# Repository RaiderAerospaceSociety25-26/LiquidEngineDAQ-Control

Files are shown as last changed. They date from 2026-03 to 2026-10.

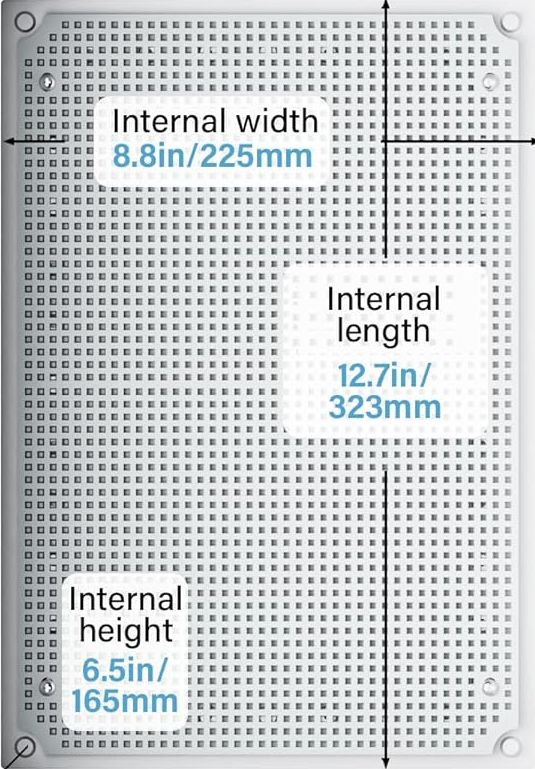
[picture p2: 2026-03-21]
hardware/layout/controlsbox_GEVEELIFE_crop.jpg

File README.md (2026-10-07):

# LiquidEngineDAQ-Control
Repository for DAQ and control system for the liquid engine and test stand being developed by Kyle Markel for the Raider Aerospace Society (RAS) PigeonWorks Liquid Engine Team during the 2025-2026 and 2026-2027 academic years.

For master to-do list, see Kanban board in Teams for the most up-to-date information.

# Firmware
## Firmware Architecture
Plan is to just use Arduino and the common setup and loop structure for the Teensys. The Nucleo will need STM32Cube IDE to be able to flash to both the M7 and M4 chip (there are other ways, but this is the easiest I think). Ideally move to something like FreeRTOS (i.e. X-CUBE-FREERTOS) for the Nucleo board eventually to potentially speed things up.

SPI communication code examples [link](https://www.makerguides.com/master-slave-spi-communication-arduino/#SPI_Master-Slave_Interfacing)

### MCU Function Divisions and Required Libraries
#### Teensy LC/TM
* Functions:
  * Obtain thrust (i.e. load cell) and thermistor data and send it to Nucleo via SPI.
#### Teensy PT
* Functions:
  * Obtain PT data and send it to Nucleo via SPI.
#### Nucleo
* Functions:
  * Receive LC/TM/PT data via two SPI connections
  * Write data to SD card
  * Actuate valves (servo-actuated ball valves) and send ignition signal based on predetermined sequences triggered by T-Beam radio over TX/RX pins
  * Sense overpressures or other issues and send alarms and/or autonomously actuate valves
  * (Maybe: execute automatic safing/depressurization procedures)

# Hardware and Firmware

### MCUs

#### Nucleo-H755ZI-Q
[STMicroelectronics Nucleo-144 H755ZI-Q](https://www.st.com/en/evaluation-tools/nucleo-h755zi-q.html)

Main MCU: STM32H755ZIT6

Secondary MCU: STM32F723IEK6 (I think)

Software required for programming: STM32MX, STM32CubeIDE, STM32CubeProg (STM32CubeProgrammer)

Flashing code to Nucleo board:
* Plug in USB cable to CN1 (the ST-LINK port).
* Have the debug configuration set in STM32CubeIDE.
* Build both M4 and M7 projects.
* Run M4 project -> this will upload the new M4 code to the M4 chip, but will also stop all operations because of the timing/sync relationship between M7 and M4.
* Run M7 project -> this will upload the new M7 code to the M7 chip and will sync and restart the M4 chip. Now all code is running correctly.
* There is probably a more streamlined way to do this so you only have to upload code once; I have not yet found it though. 

Roughly following this tutorial for coding the STM32: STM32Cube IDE tutorial for multiple cores [link](https://blog.embeddedexpert.io/?p=4075) 

Some info about setting up FreeRTOS on the Nucleo [link](https://dds-demonstrators.readthedocs.io/en/latest/Teams/2.Demonstra-Tors/7.NucleoDDS/DDSFreeRTOS.html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)

Relevant timer info [link](https://community.st.com/stm32cubemx-mcus-29/trouble-changing-timebase-to-something-other-than-systick-24703)

Info on requiring a different timebase when running with RTOS [link](https://community.st.com/stm32cubemx-mcus-29/code-generated-by-stm32cubemx-sets-the-hal-timebase-isr-priority-incorrectly-when-using-freertos-is-it-really-necessary-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)

SPI1: PT Teensy

SPI3: LC/TM Teensy

I2C1: Servo shield

PE14: Ignition relay GPIO pin

LPUART1: Radio I/O (UART tutorial with STM32: https://controllerstech.com/stm32-uart-1-configure-uart-transmit-data/)

QSPI: SD card board (CN10: 13, 15, 21, 23 | PG6, PB2, PD12, PD11)

LEDs: green (1 - PB0), red (3 - PB14), yellow (2 - PE1) [info from schematic: https://www.st.com/resource/en/schematic_pack/mb1363-h755ziq-d01_schematic.pdf]

### ADS1256 Notes
ADS1256 analog signal input maxes out at AVDD minus 2V (so 3V maximum analog signal) if using self-calibration routines with the buffer. If we have the capability to perform calibration and write calibration values directly to the register, we could bypass this and use the full range (analog signals accepted up to AVDD), but this would likely be fairly difficult. HOWEVER, it looks like the buffer is the issue. The buffer increases input impedance to lower noise/settling time/do other stuff I don't fully understand. Overall, the buffer is needed for high-output impedance sensors. With our pressure transducers, we have a 0.5V-4.5V signal. Generally, pressure transducers are relatively low impedance (mA PTs are very low impedance, mV PTs are higher impedance I think). Briefly looking up PTs, it appears that their impedances are on the order of 100 Ω, which should have no issue as the input impedance on the ADS1256, even with the buffer off, is (150 kΩ / PGA) for PGA values of 16 or lower (and we won't need a high PGA value).  Therefore, I don't think the buffer is essential. So we're good, we just have to make sure that the buffer stays off if we're measuring pressures higher than ~60%-70% of the range of the pressure transducer. Note that the ADC will require a lot more current with the buffer off. Note that the buffer is actually off by default too. Also make sure to keep the PGA low (which won't be an issue because the signal we're reading is already 0.5V-4.5V).

ADS1256 library [link](https://github.com/CuriousScientist0/ADS1256)

### T-Beam Notes
RX of T-Beam is connected to TX pin on Arduino/Nucleo, and TX of T-Beam is connected to RX pin on Arduino/Nucleo.
Works via Meshtastic.

### ADS1115 Notes
ADS1115 will be for the thermistors. Just need two resistors of known/measured resistance to create a voltage divider circuit on the breadboard to get the resistance value of the thermistor, and this value is known at a bunch of different temperatures, so the temperature can be found easily in this manner.
Thermistor link [here](https://www.automationdirect.com/adc/shopping/catalog/process_control_-a-_measurement/temperature_sensors_-a-_transmitters/temperature_sensors/ntc10k3-n38p14-01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)
Thermistor response curve [here](https://cdn.automationdirect.com/static/support/techqa/10K-3_thermistor_resistance.pdf)
Thermistor voltage divider explained [here](https://www.build-electronic-circuits.com/voltage-divider/)

### NAU7802 Notes
NAU7802 is for the load cell. It appears that the maximum excitation voltage provided by the LDO on the breakout board is 4.5 V, which is below the load cell's range of 5-10 V excitation [load cell link](https://www.amazon.com/dp/B0CPSL6KX7/ref=dp_iou_view_item?ie=UTF8&psc=1&th=1) (1000 kg, 58 mm). This should be ok, but this does introduce additional sources of error. It is also likely possible to use an external excitation supply if desired.

### Ignition Relay Notes
[Relay link](https://www.elecbee.com/en/product-detail/5v-1-channel-level-trigger-optocoupler-relay-module-high-or-low-level-trigger-relay-board-for-raspberry-pi-arduino-relay-di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)
Need to make sure the LED on the relay is functioning as expected (probably LED off to indicate relay off?).
Additionally, for safety reasons, it would be great to have a physical switch like [this](https://www.adafruit.com/product/3218) (we might already have one something like this) on the 12V supply to the relay as a redundant hardware switch. Maybe? Not sure this is 100% necessary but it would be good peace of mind and good practice.

# Docs
Pin assignments for Nucleo board are listed in the manual pg. ~38

# Operation Notes
### Data/Debugging/Flashing MCUs While Under External Power
The 5V/USB power connector trace has been cut for both Teensys (this separates USB and external power). This allows USB to be connected for data only, while the board is powered with external 5V at the same time.

For the Nucleo-144 board, follow instructions on pg. 22 (section 7.4.6) of the manual: connect the USB cable only after the board has been powered on via external power.

# Operation
For safety: when the system 

# random notes about PlatformIO and related stuff that is likely no longer relevant
To install a library in VSCode PlatformIO: Go to PlatformIO Home -> Libraries. Then search for the library and add it. This will add the library as a reference in the `lib_deps` section of the `platformio.ini` file and will add the library to the `<Project>/.pio/libdeps/<chipname>/` folder. Libraries are generally installed per-project like this unless configured otherwise. For already-included libraries (such as `Wire` or `SPI` for the Teensy), you can simply add the library definition directly to the `lib_deps` section (I think?), or maybe this is not needed and you can just do the usual `#include` entry at the top of your code. (If needed, you can directly reference the library GitHub in the `lib_deps` section instead, and this will install the library in the `.pio` folder.

Basics of PlatformIO for Teensy [here](https://forum.pjrc.com/index.php?threads/tutorial-how-to-use-platformio-visual-code-studio-for-teensy.66674/)

There is an STM32 plugin for VSCode with info [here](https://www.st.com/content/st_com/en/campaigns/stm32-vs-code-extension-z11.html)

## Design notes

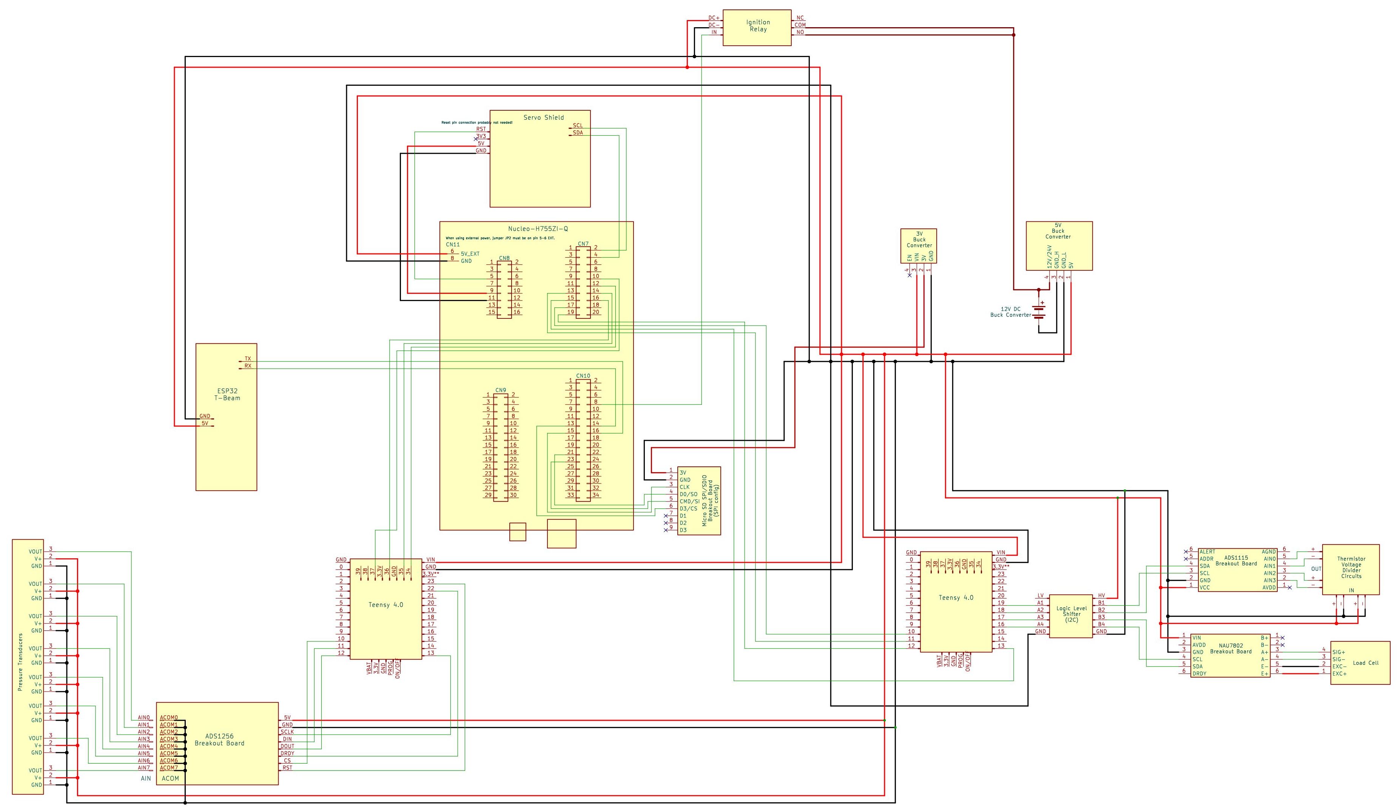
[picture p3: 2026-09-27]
hardware/Liquid Engine DAQ Diagram/Liquid Engine DAQ Diagram_2_crop.jpg

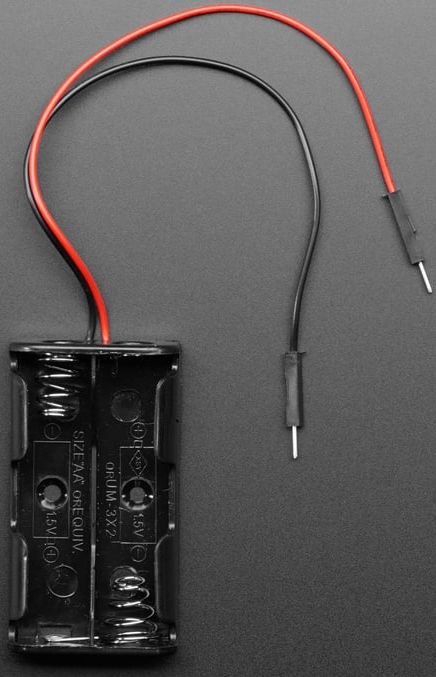
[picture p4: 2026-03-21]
hardware/layout/aa batt holder.jpg

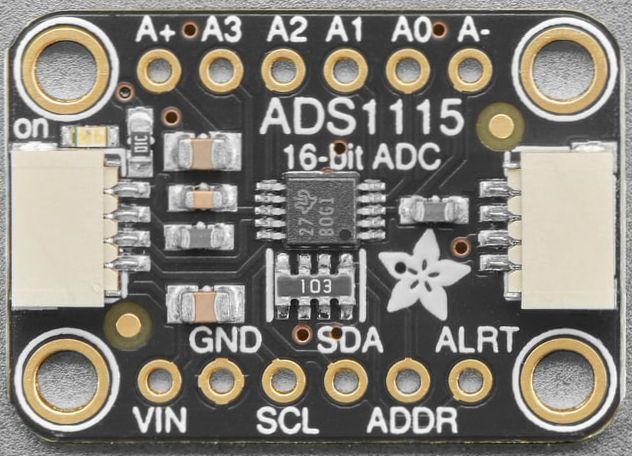
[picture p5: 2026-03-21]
hardware/layout/ads1115.jpg

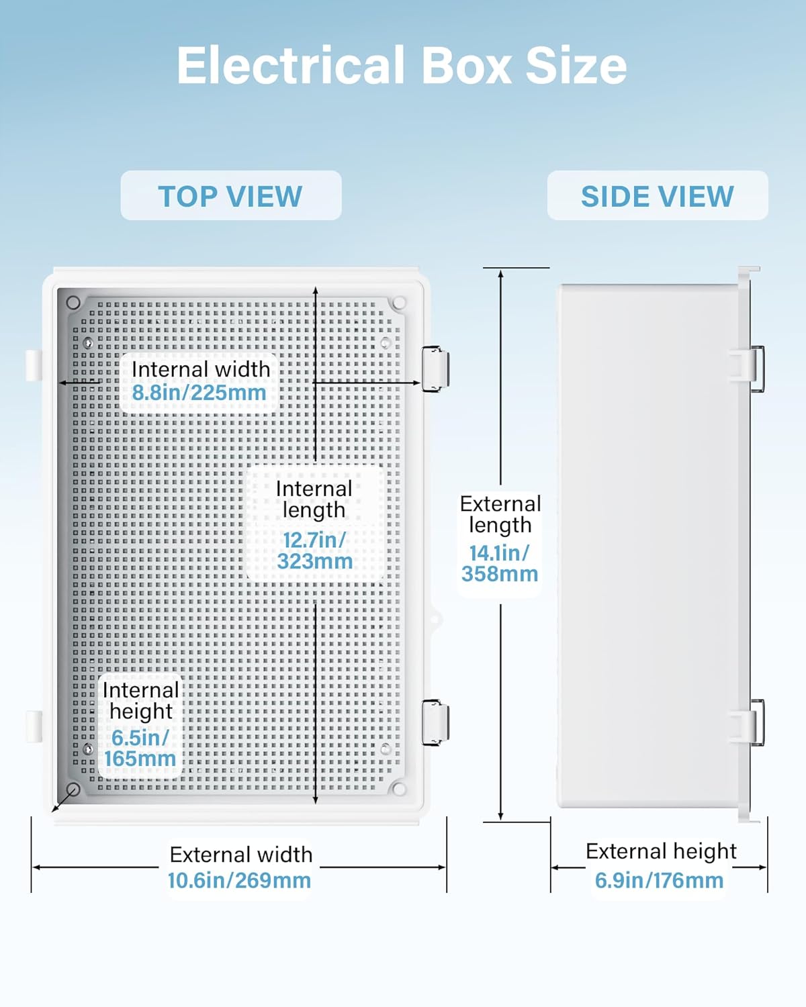
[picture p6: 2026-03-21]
hardware/layout/controlsbox_GEVEELIFE.jpg

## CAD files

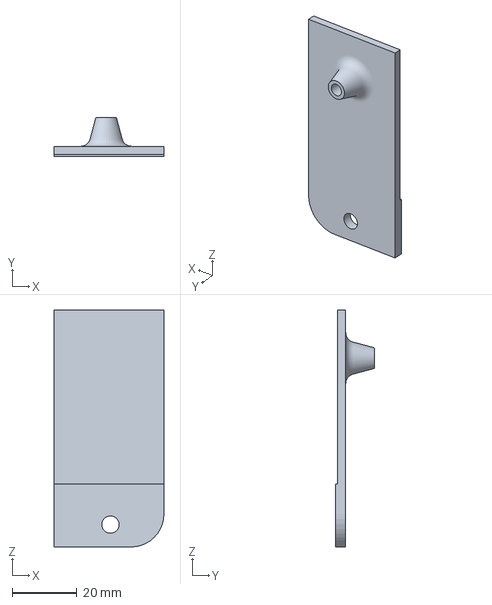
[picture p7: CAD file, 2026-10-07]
hardware/ElectronicsMountingPlate_PrintTest4.3MF
33.9 x 12.1 x 73.1 mm

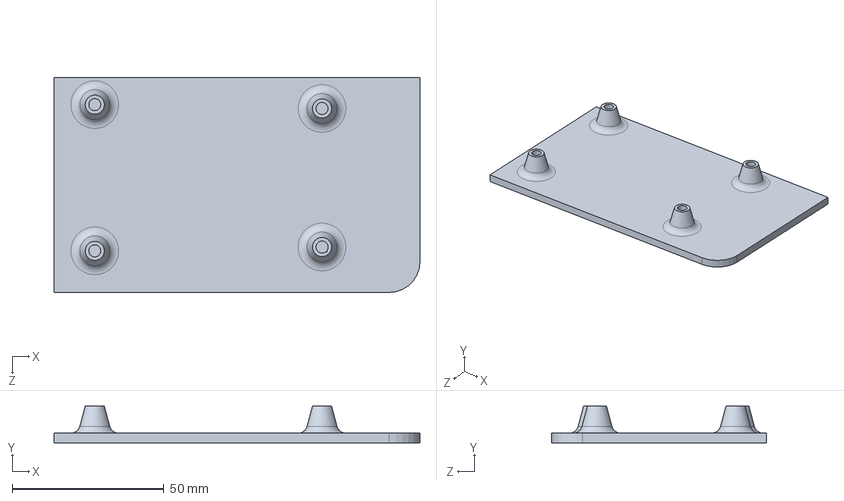
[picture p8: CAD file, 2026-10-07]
hardware/ElectronicsMountingPlate_PrintTest6.SLDPRT
120.8 x 12.1 x 70.9 mm

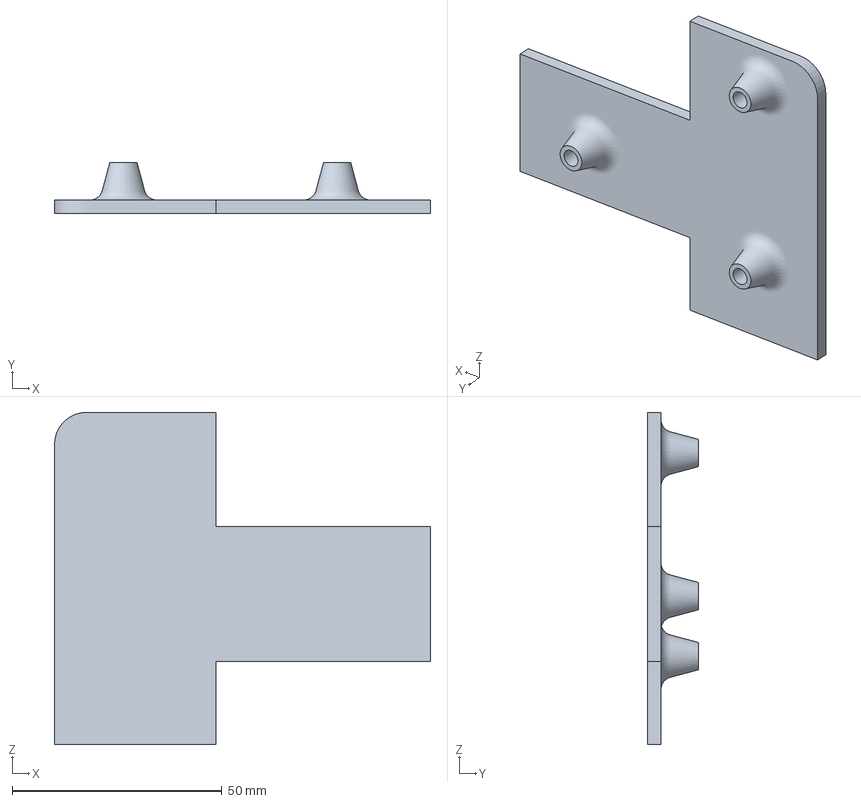
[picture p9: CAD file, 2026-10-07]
hardware/ElectronicsMountingPlate_PrintTest1.3MF
89.7 x 12.1 x 79.3 mm

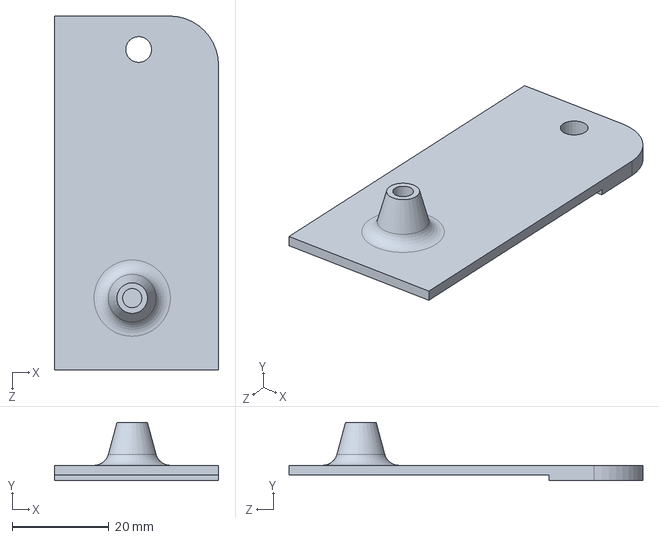
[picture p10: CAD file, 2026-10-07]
hardware/ElectronicsMountingPlate_PrintTest_4-5.SLDPRT
33.9 x 12.1 x 73.1 mm

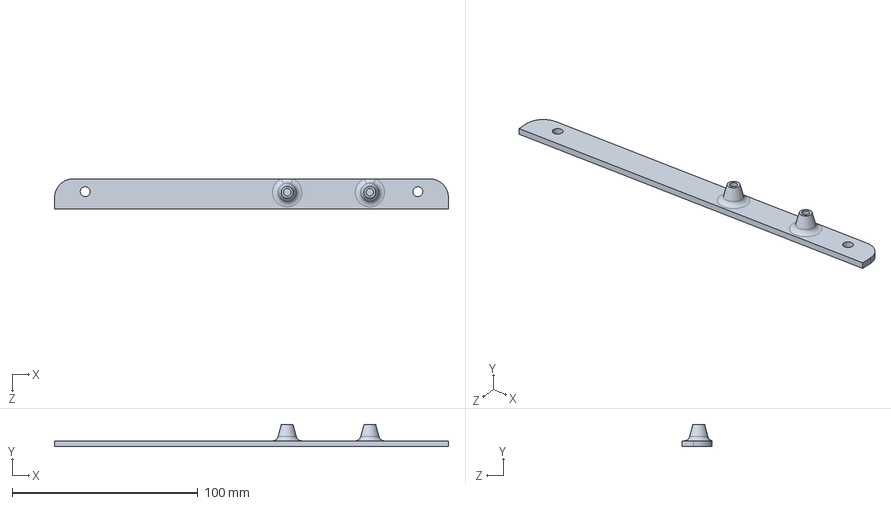
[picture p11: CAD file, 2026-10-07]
hardware/ElectronicsMountingPlate_PrintTest3.SLDPRT
212.1 x 12.1 x 16.4 mm

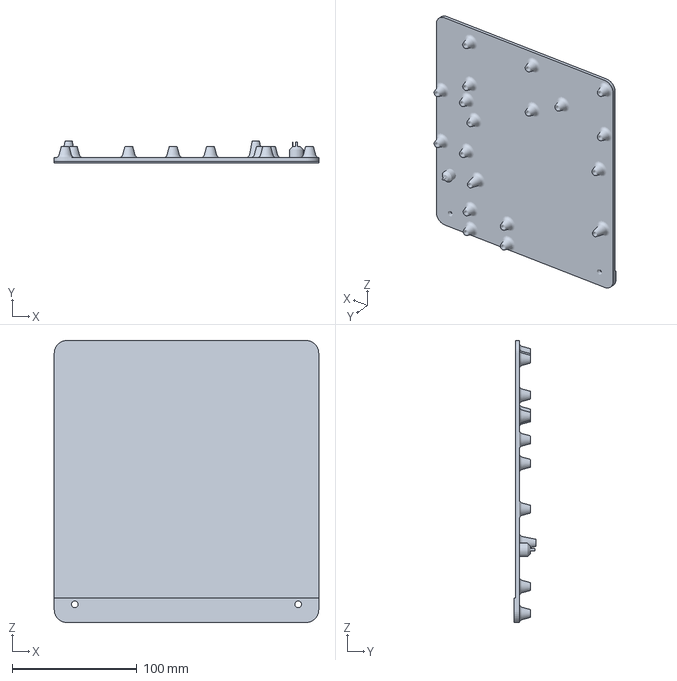
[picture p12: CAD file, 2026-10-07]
hardware/ElectronicsMountingPlate_FINAL.3MF
212.1 x 17.7 x 226.1 mm

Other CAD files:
hardware/ElectronicsMountingPlate_PrintTest5.3MF
hardware/ElectronicsMountingPlate_PrintTest2.3MF
hardware/ElectronicsMountingPlate_PrintTest_1-2.SLDPRT
hardware/ElectronicsMountingPlate.SLDPRT
hardware/ElectronicsMountingPlate_PrintTest3.3MF
hardware/ElectronicsMountingPlate_PrintTest6.3MF

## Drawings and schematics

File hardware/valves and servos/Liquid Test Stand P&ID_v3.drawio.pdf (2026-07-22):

## Fill

## Combustion

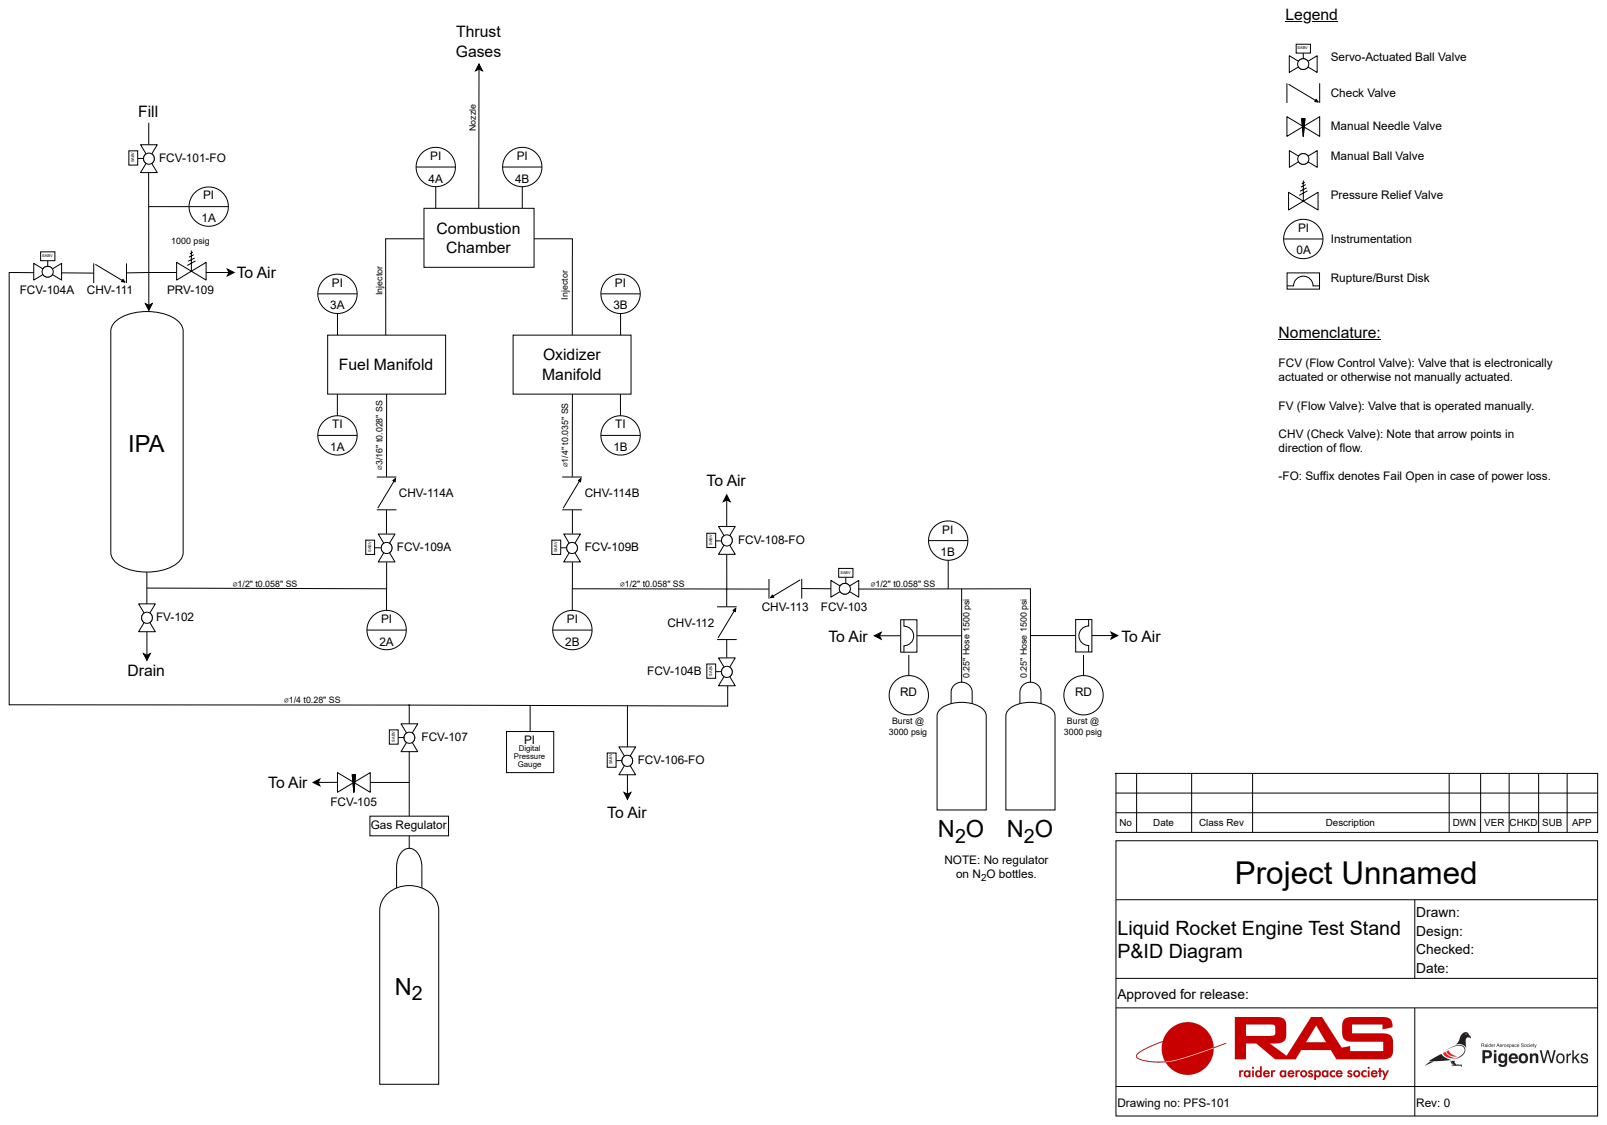
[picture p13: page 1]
IPA; Drain; Fuel Manifold; Oxidizer; Manifold; Chamber; FCV-101-FO; FCV-104A; CHV-112; FCV-104B; CHV-113 FCV-103; Thrust Gases; FCV-107; Project Unnamed; Drawn: Design: Checked: Date:; Drawing no: PFS-101; Rev: 0; Date; Class Rev; Description; DWN; VER; CHKD; SUB; APP; PRV-109; FCV-109A; FCV-109B; CHV-114A; CHV-114B; To Air; 0.25" Hose 1500 psi; Injector; Nozzle; Burst @ 3000 psig; Gas Regulator; CHV-111; FCV-108-FO; FCV-106-FO; FCV-105; SABV; 1000 psig; Check Valve; Legend; Instrumentation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

SABV
Servo-Actuated Ball Valve

Manual Needle Valve

Manual Ball Valve

Pressure Relief Valve

Rupture/Burst Disk

FCV (Flow Control Valve): Valve that is electronically
actuated or otherwise not manually actuated.

FV (Flow Valve): Valve that is operated manually.

CHV (Check Valve): Note that arrow points in
direction of flow.

-FO: Suffix denotes Fail Open in case of power loss.

NOTE: No regulator
on N2O bottles.

Liquid Rocket Engine Test Stand
P&ID Diagram

Approved for release:

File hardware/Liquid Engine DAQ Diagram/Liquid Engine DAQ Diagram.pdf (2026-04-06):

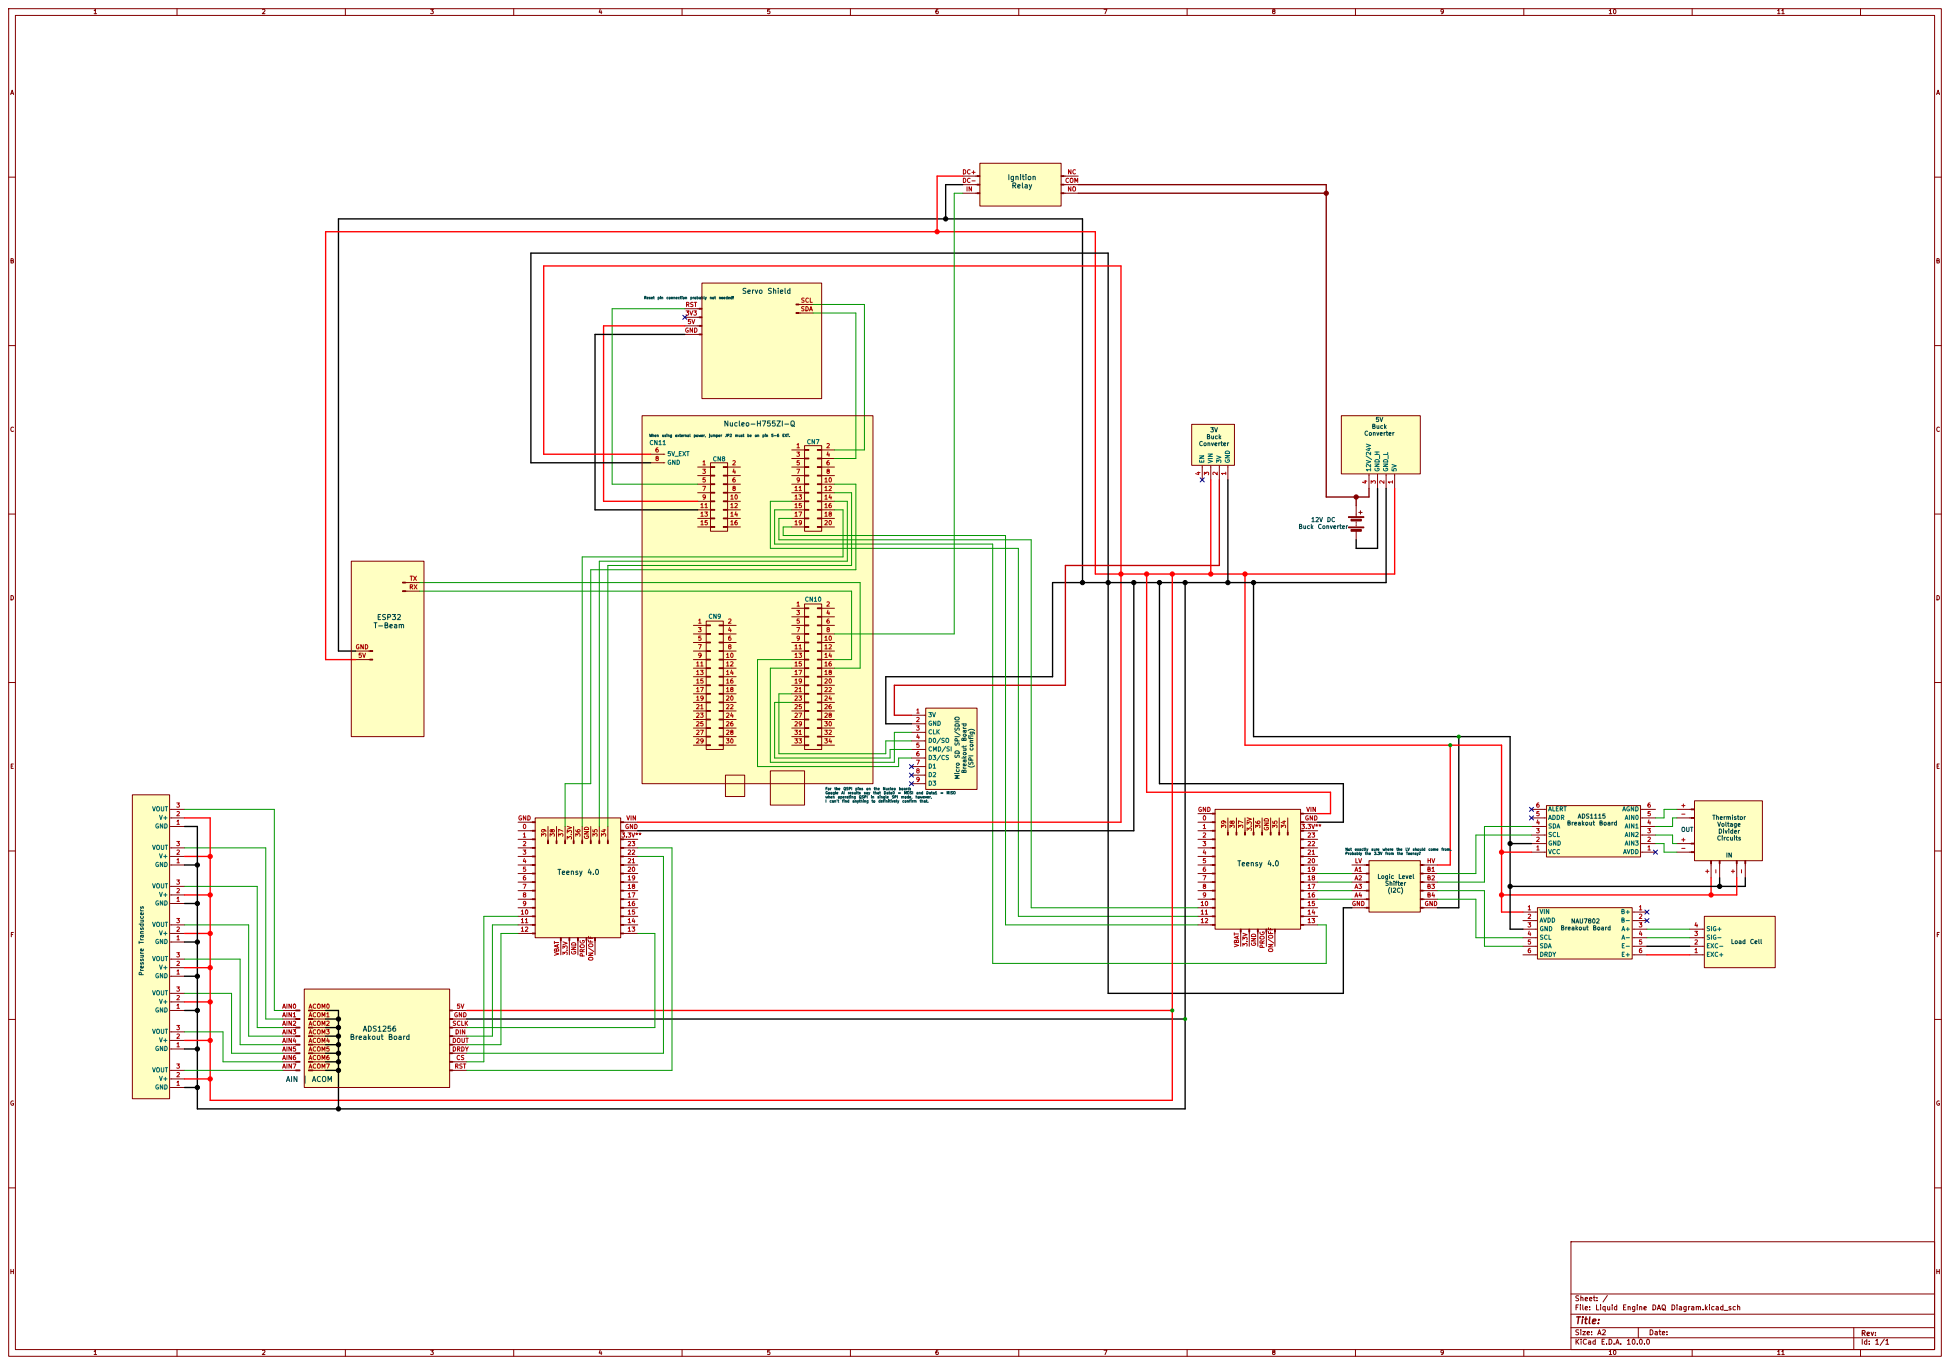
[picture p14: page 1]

T-Beam Pressure Transducers 16x2 LCD

Reset pin connection probably not needed!

When using external power, jumper JP2 must be on pin 5-6 EXT.

For the QSPI pins on the Nucleo board: Google AI results say that Data0 = MOSI and Data1 = MISO

when operating QSPI in single SPI mode, however,

Thermistor Voltage Divider Circuits

- 3.3V 393837363534 GND 3.3V GND ON/OFF VBAT PROG

SCL 3 | 3

Not exactly sure where the LV should come from. Probably the 3.3V from the Teensy? Logic Level Shifter (I2C)
A4 GND

NAU7802 Breakout Board AIN | ACOM

Sheet: /
File: Liquid Engine DAQ Diagram.kicad_sch
Title:

Size: A2 | Rev:
KiCad E.D.A. 10.0.0 | Id: 1/1

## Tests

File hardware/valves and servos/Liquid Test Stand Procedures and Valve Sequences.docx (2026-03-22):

LIQUID TEST STAND PROCEDURES AND VALVE SEQUENCES

Default state prior to filling IPA tank:

- FV-110: Closed
- FCV-107A: Closed
- FCV-109: Closed
- FV-101: Open (probably either)
- FCV-104A: Closed
- FCV-104B: Closed
- FCV-102: Closed
- FCV-107B: Closed
- FCV-105A: probably either
- FCV-105B: probably either

Fill IPA tank:

- Open FV-101.
- Ensure FV-110 is closed.
- Ensure FCV-107A, FCV-109, and FCV-107B are closed.
- Ensure FCV-104A is closed.
- Fill IPA tank to desired level by pouring in IPA from the fitting on top of the tank. Once IPA tank is filled, close FV-101.
- Set the regulator on the N2 bottle to desired pressure to pressurize the IPA tank.
- Open FCV-109 and FCV-107A to pressurize the IPA tank.

Pressurize nitrous line:

- Ensure nitrous line has already been purged.
- Ensure FCV-107B and FCV-104B are closed.
- Open FCV-102.

Fire:

- Set needle valves to initial value.
- Enter startup sequence. The following things happen very quickly/overlapped in time:
  - Open FCV-104A and FCV-104B at the same time.
  - Fire ignitor.
  - Ramp up needle valve openings if needed (for gradual start).

Immediately post-fire:

- Close FCV-102 and FCV-104A.

Post-fire purge:

- Ensure FCV-102 is closed.
- Open FCV-104A, FCV-104B, FCV-107A, and FCV-107B simultaneously, purging lines with the remaining N2 pressure in the IPA tank.
- If additional purging is needed using gas from the N2 tank:
  - Open FCV-109, and once finished, close FCV-109.

Post-purge return to default state:

- Ensure FCV-109 is closed.
- Close FCV-107A, FCV-107B.
- Close FCV-104A, 104B.
- Optionally close FCV-105A, FCV-105B.

Approach the test stand:

- Visually verify safe state.
- Open FV-110 if needed to drain out any remaining fuel/residue. Close FV-110 once finished.
- Ensure test stand is ready for next fire.

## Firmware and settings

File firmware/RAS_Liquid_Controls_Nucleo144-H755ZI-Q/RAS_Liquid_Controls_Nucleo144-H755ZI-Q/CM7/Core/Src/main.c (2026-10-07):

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
/* Includes ------------------------------------------------------------------*/
#include "main.h"
#include "FreeRTOS.h"
#include "cmsis_os2.h"

/* USER CODE BEGIN PD */

/* DUAL_CORE_BOOT_SYNC_SEQUENCE: Define for dual core boot synchronization    */
/*                             demonstration code based on hardware semaphore */
/* This define is present in both CM7/CM4 projects                            */
/* To comment when developping/debugging on a single core                     */
#define DUAL_CORE_BOOT_SYNC_SEQUENCE

#if defined(DUAL_CORE_BOOT_SYNC_SEQUENCE)
#ifndef HSEM_ID_0
#define HSEM_ID_0 (0U) /* HW semaphore 0*/
#endif
#endif /* DUAL_CORE_BOOT_SYNC_SEQUENCE */

/* USER CODE END PD */


I2C_HandleTypeDef hi2c1;

UART_HandleTypeDef hlpuart1;

SPI_HandleTypeDef hspi1;
SPI_HandleTypeDef hspi3;

/* Definitions for defaultTask */
osThreadId_t defaultTaskHandle;
const osThreadAttr_t defaultTask_attributes = {
  .name = "defaultTask",
  .stack_size = 128 * 4,
  .priority = (osPriority_t) osPriorityNormal,
};
void SystemClock_Config(void);
static void MPU_Config(void);
static void MX_GPIO_Init(void);
static void MX_I2C1_Init(void);
static void MX_LPUART1_UART_Init(void);
static void MX_SPI1_Init(void);
static void MX_SPI3_Init(void);
void StartDefaultTask(void *argument);

/**
  * @brief  The application entry point.
  * @retval int
  */
int main(void)
{

/* USER CODE BEGIN Boot_Mode_Sequence_0 */
#if defined(DUAL_CORE_BOOT_SYNC_SEQUENCE)
  int32_t timeout;
#endif /* DUAL_CORE_BOOT_SYNC_SEQUENCE */
/* USER CODE END Boot_Mode_Sequence_0 */

  /* MPU Configuration--------------------------------------------------------*/
  MPU_Config();

/* USER CODE BEGIN Boot_Mode_Sequence_1 */
#if defined(DUAL_CORE_BOOT_SYNC_SEQUENCE)
  /* Wait until CPU2 boots and enters in stop mode or timeout*/
  timeout = 0xFFFF;
  while((__HAL_RCC_GET_FLAG(RCC_FLAG_D2CKRDY) != RESET) && (timeout-- > 0));
  if ( timeout < 0 )
  {
	  Error_Handler();
  }
#endif /* DUAL_CORE_BOOT_SYNC_SEQUENCE */
/* USER CODE END Boot_Mode_Sequence_1 */
  /* MCU Configuration--------------------------------------------------------*/

  /* Reset of all peripherals, Initializes the Flash interface and the Systick. */
  HAL_Init();

  /* Configure the system clock */
  SystemClock_Config();
/* USER CODE BEGIN Boot_Mode_Sequence_2 */

#if defined(DUAL_CORE_BOOT_SYNC_SEQUENCE)
/* When system initialization is finished, Cortex-M7 will release Cortex-M4 by means of
HSEM notification */
/*HW semaphore Clock enable*/
__HAL_RCC_HSEM_CLK_ENABLE();
/*Take HSEM */
HAL_HSEM_FastTake(HSEM_ID_0);
/*Release HSEM in order to notify the CPU2(CM4)*/
HAL_HSEM_Release(HSEM_ID_0,0);
/* wait until CPU2 wakes up from stop mode */
timeout = 0xFFFF;
while((__HAL_RCC_GET_FLAG(RCC_FLAG_D2CKRDY) == RESET) && (timeout-- > 0));
if ( timeout < 0 )
{
	Error_Handler();
}
#endif /* DUAL_CORE_BOOT_SYNC_SEQUENCE */
/* USER CODE END Boot_Mode_Sequence_2 */

  /* Initialize all configured peripherals */
  MX_GPIO_Init();
  MX_I2C1_Init();
  MX_LPUART1_UART_Init();
  MX_SPI1_Init();
  MX_SPI3_Init();
  /* USER CODE BEGIN 2 */
  //LED DEBUG
  //HAL_GPIO_WritePin(LEDGM7_GPIO_Port, LEDGM7_Pin, GPIO_PIN_SET);   /* green solid */
  /* USER CODE END 2 */

  /* Init scheduler */
  osKernelInitialize();

  /* USER CODE BEGIN RTOS_MUTEX */
  /* add mutexes, ... */
  /* USER CODE END RTOS_MUTEX */

  /* USER CODE BEGIN RTOS_SEMAPHORES */
  /* add semaphores, ... */
  /* USER CODE END RTOS_SEMAPHORES */

  /* USER CODE BEGIN RTOS_TIMERS */
  /* start timers, add new ones, ... */
  /* USER CODE END RTOS_TIMERS */

  /* USER CODE BEGIN RTOS_QUEUES */
  /* add queues, ... */
  /* USER CODE END RTOS_QUEUES */

  /* Create the thread(s) */
  /* creation of defaultTask */
  defaultTaskHandle = osThreadNew(StartDefaultTask, NULL, &defaultTask_attributes);

  /* USER CODE BEGIN RTOS_THREADS */
  /* add threads, ... */
  /* USER CODE END RTOS_THREADS */

  /* USER CODE BEGIN RTOS_EVENTS */
  /* add events, ... */
  /* USER CODE END RTOS_EVENTS */

  /* Start scheduler */
  osKernelStart();

  /* We should never get here as control is now taken by the scheduler */

  /* Infinite loop */
  /* USER CODE BEGIN WHILE */
  while (1)
  {
    /* USER CODE END WHILE */

    /* USER CODE BEGIN 3 */
  }
  /* USER CODE END 3 */
}

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
/* USER CODE BEGIN Header_StartDefaultTask */
/**
  * @brief  Function implementing the defaultTask thread.
  * @param  argument: Not used
  * @retval None
  */
/* USER CODE END Header_StartDefaultTask */
void StartDefaultTask(void *argument)
{
  /* USER CODE BEGIN 5 */
  /* Infinite loop */
  for(;;)
  {
	  HAL_GPIO_TogglePin(LEDYM7_GPIO_Port, LEDYM7_Pin);
	  HAL_GPIO_TogglePin(LEDRM7_GPIO_Port, LEDRM7_Pin);
	  HAL_Delay(100);
	  //	  HAL_GPIO_WritePin(LEDRM7_GPIO_Port, LEDRM7_Pin, GPIO_PIN_SET);
  }
  /* USER CODE END 5 */
}

 /* MPU Configuration */

void MPU_Config(void)
{
  MPU_Region_InitTypeDef MPU_InitStruct = {0};

  /* Disables the MPU */
  HAL_MPU_Disable();

  /** Initializes and configures the Region and the memory to be protected
  */
  MPU_InitStruct.Enable = MPU_REGION_ENABLE;
  MPU_InitStruct.Number = MPU_REGION_NUMBER0;
  MPU_InitStruct.BaseAddress = 0x0;
  MPU_InitStruct.Size = MPU_REGION_SIZE_4GB;
  MPU_InitStruct.SubRegionDisable = 0x87;
  MPU_InitStruct.TypeExtField = MPU_TEX_LEVEL0;
  MPU_InitStruct.AccessPermission = MPU_REGION_NO_ACCESS;
  MPU_InitStruct.DisableExec = MPU_INSTRUCTION_ACCESS_DISABLE;
  MPU_InitStruct.IsShareable = MPU_ACCESS_SHAREABLE;
  MPU_InitStruct.IsCacheable = MPU_ACCESS_NOT_CACHEABLE;
  MPU_InitStruct.IsBufferable = MPU_ACCESS_NOT_BUFFERABLE;

  HAL_MPU_ConfigRegion(&MPU_InitStruct);
  /* Enables the MPU */
  HAL_MPU_Enable(MPU_PRIVILEGED_DEFAULT);

}

/**
  * @brief  Period elapsed callback in non blocking mode
  * @note   This function is called  when TIM6 interrupt took place, inside
  * HAL_TIM_IRQHandler(). It makes a direct call to HAL_IncTick() to increment
  * a global variable "uwTick" used as application time base.
  * @param  htim : TIM handle
  * @retval None
  */
void HAL_TIM_PeriodElapsedCallback(TIM_HandleTypeDef *htim)
{
  if (htim->Instance == TIM6)
  {
    HAL_IncTick();
  }
}

/**
  * @brief  This function is executed in case of error occurrence.
  * @retval None
  */
void Error_Handler(void)
{
  /* USER CODE BEGIN Error_Handler_Debug */

  /* User can add his own implementation to report the HAL error return state */
  __disable_irq();
  while (1)
  {
  }
  /* USER CODE END Error_Handler_Debug */
}
#ifdef USE_FULL_ASSERT
/**
  * @brief  Reports the name of the source file and the source line number
  *         where the assert_param error has occurred.
  * @param  file: pointer to the source file name
  * @param  line: assert_param error line source number
  * @retval None
  */
void assert_failed(uint8_t *file, uint32_t line)
{
  /* USER CODE BEGIN 6 */
  /* User can add his own implementation to report the file name and line number,
     ex: printf("Wrong parameters value: file %s on line %d\r\n", file, line) */
  /* USER CODE END 6 */
}
#endif /* USE_FULL_ASSERT */

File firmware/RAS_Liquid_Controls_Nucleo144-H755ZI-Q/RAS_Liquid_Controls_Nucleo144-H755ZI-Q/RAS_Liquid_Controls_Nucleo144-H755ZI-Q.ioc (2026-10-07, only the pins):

Mcu.UserName=STM32H755ZITx
PA10.Signal=LPUART1_RX
PA4.Signal=SPI3_NSS
PA5.Signal=SPI1_SCK
PA6.Signal=SPI1_MISO
PA9.Signal=LPUART1_TX
PB0.GPIO_Label=LEDGM4
PB0.Signal=GPIO_Output
PB10.Signal=QUADSPI_BK1_NCS
PB14.GPIO_Label=LEDRM7
PB14.Signal=GPIO_Output
PB6.Signal=I2C1_SCL
PB7.Signal=I2C1_SDA
PC10.Signal=SPI3_SCK
PE1.GPIO_Label=LEDYM7
PE1.Signal=GPIO_Output
PF10.Signal=QUADSPI_CLK
PF8.Signal=QUADSPI_BK1_IO0
PF9.Signal=QUADSPI_BK1_IO1

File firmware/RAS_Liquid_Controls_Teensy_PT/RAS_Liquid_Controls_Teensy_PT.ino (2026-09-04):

#include <SPI.h>

// ----------------------------- ADS1256 (8-CHANNEL ADC FOR PRESSURE TRANSDUCERS) -----------------------------------
#include <ADS1256.h> // library documentation: https://github.com/CuriousScientist0/ADS1256/blob/main/extras/ADS1256_ArduinoLibrary_Documentation_20251023.pdf

// ---------------- HELPER DEFINITIONS ----------------
//Differential inputs
// #define DIFF_0_1 0b00000001 //A0 + A1 as differential input
// #define DIFF_2_3 0b00100011 //A2 + A3 as differential input
// #define DIFF_4_5 0b01000101 //A4 + A5 as differential input
// #define DIFF_6_7 0b01100111 //A6 + A7 as differential input

//Single-ended inputs
// #define SING_0 0b00001111 //A0 + GND (common) as single-ended input
// #define SING_1 0b00011111 //A1 + GND (common) as single-ended input
// #define SING_2 0b00101111 //A2 + GND (common) as single-ended input
// #define SING_3 0b00111111 //A3 + GND (common) as single-ended input
// #define SING_4 0b01001111 //A4 + GND (common) as single-ended input
// #define SING_5 0b01011111 //A5 + GND (common) as single-ended input
// #define SING_6 0b01101111 //A6 + GND (common) as single-ended input
// #define SING_7 0b01111111 //A7 + GND (common) as single-ended input

//PGA settings			  //Input voltage range
#define PGA_1 0b00000000  //± 5 V
#define PGA_2 0b00000001  //± 2.5 V
#define PGA_4 0b00000010  //± 1.25 V
#define PGA_8 0b00000011  //± 625 mV
#define PGA_16 0b00000100 //± 312.5 mV
#define PGA_32 0b00000101 //+ 156.25 mV
#define PGA_64 0b00000110 //± 78.125 mV

//Datarate						  //DEC
#define DRATE_30000SPS 0b11110000 //240
#define DRATE_15000SPS 0b11100000 //224
#define DRATE_7500SPS 0b11010000  //208
#define DRATE_3750SPS 0b11000000  //192
#define DRATE_2000SPS 0b10110000  //176
#define DRATE_1000SPS 0b10100001  //161
#define DRATE_500SPS 0b10010010   //146
#define DRATE_100SPS 0b10000010   //130
#define DRATE_60SPS 0b01110010    //114
#define DRATE_50SPS 0b01100011    //99
#define DRATE_30SPS 0b01010011    //83
#define DRATE_25SPS 0b01000011    //67
#define DRATE_15SPS 0b00110011    //51
#define DRATE_10SPS 0b00100011    //35
#define DRATE_5SPS 0b00010011     //19
#define DRATE_2SPS 0b00000011     //3

//Status register
#define BITORDER_MSB 0
#define BITORDER_LSB 1
#define ACAL_DISABLED 0
#define ACAL_ENABLED 1
#define BUFFER_DISABLED 0
#define BUFFER_ENABLED 1

//Register addresses
#define STATUS_REG 0x00
#define MUX_REG 0x01
#define ADCON_REG 0x02
#define DRATE_REG 0x03
#define IO_REG 0x04
#define OFC0_REG 0x05
#define OFC1_REG 0x06
#define OFC2_REG 0x07
#define FSC0_REG 0x08
#define FSC1_REG 0x09
#define FSC2_REG 0x0A

//Command definitions
#define WAKEUP 0b00000000
#define RDATA 0b00000001
#define RDATAC 0b00000011
#define SDATAC 0b00001111
#define RREG 0b00010000
#define WREG 0b01010000
#define SELFCAL 0b11110000
#define SELFOCAL 0b11110001
#define SELFGCAL 0b11110010
#define SYSOCAL 0b11110011
#define SYSGCAL 0b11110100
#define SYNC 0b11111100
#define STANDBY 0b11111101
#define RESET 0b11111110
//--------------------------------

//pin definitions
#define SPI_MOSI 11
#define SPI_MISO 12
#define SPI_SCK 13
#define USE_SPI SPI1
#define DRDY 7
#define SYNC 8
#define CS 10
#define VREF_M 2.500 //measured VREF value

#define BUF_SET = BUFFER_DISABLED //Set buffer off (0) or on (1). BUFFER MUST BE TURNED OFF FOR READING +4.5V FROM RATIOMETRIC PT!
#define PGA_SET PGA_1 //Set PGA (programmable gain amplifier) to 1 to measure ± 5 V
//Note: datarate SPS numbers are only for single-input measurement. If more inputs are used, above 100 SPS, the true SPS is much lower due to the multiplexer having to cycle through inputs: 30000 SPS = 4374 Hz, 2000 SPS = 1438 Hz, 500 SPS = 456 Hz, and so on.
#define DRATE_SET DRATE_2000SPS //set to 2000 sps for now
//int singleEndedChannels[8] = {SING_0, SING_1, SING_2, SING_3, SING_4, SING_5, SING_6, SING_7}; //Array to store the single-ended channels
//------------------------------------------------------------------------------------------------------------------

//Create ADS1256 object. (DRDY, RESET, SYNC(PDWN), CS, VREF(float)) [for Teensy 4.0]. Measure VREF; if it is not 2.500 exactly, measure it with a multimeter and input it correctly here; this is essential for accurachy.
ADS1256 PT_ADC(DRDY, ADS1256::PIN_UNUSED, SYNC, CS, VREF_M, &USE_SPI);

int num = 0;

void setup() {
  // LED BLINK AND SETUP BEGIN CONFIRMATION
  Serial.begin(9600);
  Serial.println("Begin setup");
  pinMode(LED_BUILTIN, OUTPUT); //LED pin setup
  for (int i = 0; i < 5; i++) { digitalWrite(LED_BUILTIN, HIGH); delay(100); digitalWrite(LED_BUILTIN, LOW); delay(150); } //LED rapid flash 5 times

  // ----------------------------- INITIALIZE ADS1256 -----------------------------------
  //initialize
  PT_ADC.InitializeADC();

  //settings
  PT_ADC.setBuffer(BUFFER_DISABLED); //set buffer; ensure buffer is turned off for reading +4.5V from ratiometric PT
  uint8_t buffer_val = PT_ADC.getBuffer(); //get buffer
  Serial.print("Buffer value: ");
  Serial.println(buffer_val);
  PT_ADC.setPGA(PGA_SET); //set PGA
  PT_ADC.setDRATE(DRATE_SET); //set data rate

  //read
  long dataTest = PT_ADC.cycleSingle(); //cycleSingle() returns a 24 bit signed value converted to a long, and cycles through channels 0 -> 7 (multiplexing); as far as I can tell, each call of this function returns the long value of a single channel, and it just loops through the channels with each call of this function (not entirely sure though)
  Serial.println(dataTest);
  PT_ADC.stopConversion(); //conversion must be stopped after reading is no longer necessary

  //note setup complete
  Serial.println("PT setup complete.");
  for (int i = 0; i < 3; i++) { digitalWrite(LED_BUILTIN, HIGH); delay(500); digitalWrite(LED_BUILTIN, LOW); delay(250); } //LED 0.5-second flash 3 times
  // ------------------------------------------------------------------------------------

}

void loop() {
  if (num < 1000) {
    long dataTest = PT_ADC.cycleSingle(); //cycleSingle() returns a 24 bit signed value converted to a long, and cycles through channels 0 -> 7 (multiplexing); as far as I can tell, each call of this function returns the long value of a single channel, and it just loops through the channels with each call of this function (not entirely sure though)
    Serial.println(dataTest);
    num++;
  }
  else if (num == 1000) { PT_ADC.stopConversion(); }


}

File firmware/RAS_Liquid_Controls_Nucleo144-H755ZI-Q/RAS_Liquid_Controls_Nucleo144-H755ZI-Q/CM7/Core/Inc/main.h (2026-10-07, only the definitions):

#define LEDRM7_Pin GPIO_PIN_14
#define LEDRM7_GPIO_Port GPIOB
#define LEDYM7_Pin GPIO_PIN_1
#define LEDYM7_GPIO_Port GPIOE

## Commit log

2025-11-12 finished data and config reading
    - finished TestFire object creation functionality
    - added a second test data Excel sheet to ensure that functionality works
    - todo: start on characterization code
    [Liquid Engine DAQ Diagram.kicad_pcb, Liquid Engine DAQ Diagram.kicad_sch]
2026-01-18 updated folders and added code from 24-25
    [Liquid Engine DAQ Diagram.kicad_pcb, Liquid Engine DAQ Diagram.kicad_sch]
2026-03-21 updated files and created platformio projects for microcontrollers
    [Liquid Engine DAQ Diagram.kicad_sch]
2026-03-21 updated circuit diagram, fixed firmware project folder, added tbeam pinout
    [Liquid Engine DAQ Diagram.kicad_sch]
2026-03-22 updated circuit diagram
    - Tbeam powered using 5V, not 3V
    [Liquid Engine DAQ Diagram.kicad_sch]
2026-03-22 added P&ID and valve sequence info
2026-03-23 updated circuit diagram to reflect updates and actual solder connections
    [Liquid Engine DAQ Diagram.kicad_sch]
2026-04-06 updated wiring diagram and switched back to Arduino IDE for code
    [Liquid Engine DAQ Diagram.kicad_sch]

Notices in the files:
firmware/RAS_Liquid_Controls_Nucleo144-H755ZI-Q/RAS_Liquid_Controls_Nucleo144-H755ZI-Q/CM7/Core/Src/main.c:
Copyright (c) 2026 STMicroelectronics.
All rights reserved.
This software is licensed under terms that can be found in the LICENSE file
